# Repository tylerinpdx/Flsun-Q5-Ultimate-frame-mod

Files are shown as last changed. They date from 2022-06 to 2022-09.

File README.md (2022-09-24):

# Flsun-Q5-Ultimate-frame-mod
If you need elp or have questions, ty88#4122

The squishy wobbly motion system on the Q5 left a lot to be desired soo...

## stage 2  

keep In mind my effector is heavy ish. 182G+ 

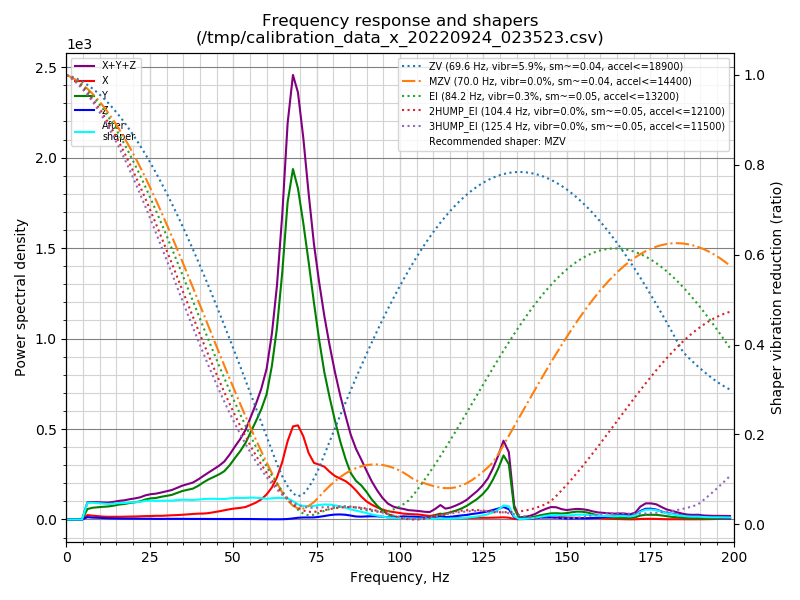
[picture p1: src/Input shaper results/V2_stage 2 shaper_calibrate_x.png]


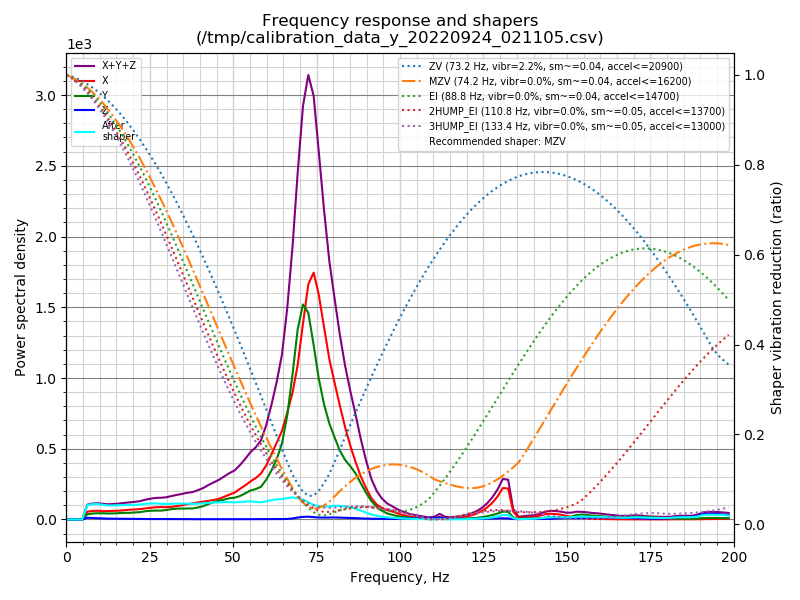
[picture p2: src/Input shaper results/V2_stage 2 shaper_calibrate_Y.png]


#### Yes this really did come from a Q5!

 

### stock tower support next to upgrade 

 

 The belt now goes all the way through the frame and into a bottom plate,
 
 Idler is held on both sides, none of that cantilever nonsense. 

 

 
In this picture the Alpha tower carriage is bottomed out against bottom tower support,
this upgrade is not supposed to reduce max printable radius but Is this **highly recommended** to reduce it to at least 96MM.

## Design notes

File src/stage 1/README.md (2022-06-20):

# Bill of materials, printing instructions and Install
The 2020 extrusion from the frame needs to fit inside the bottom tower support, so there are multiple tolerance versions.

The Idler pulley also has multiple tolerance versions, the pulley needs to have little play side to 
side otherwise it's going to rattle and make a lot of noise.

The Idler plate has a hole for a 35mm long M5 Fastener, that's should be the right size for the fastener to cut its own thread.
You could also use a 5 mm shaft.

## BOM for stage 1
- M5x16MM 12.9 12X  

- M5 t-nuts 12X These must be the larger size ones, not those twist-in nonsense things. 

- M4x50MM 12.9 6X Head diameter 7mm

- M4x22MM 12.9 3X head diameter 7 mm 

- **optional** but recommended M4 washer 9X   9 mm max diameter, max height 1.2mm

- M4 nut 9x

- M5x35MM 3X   The material doesn't matter as long as it's not pot metal.

- GT2 20T 5MM bearing idler 3X  very important, width is 8.5 mm 

- rubber feet that came with the printer and the fasteners that held the feet on. 

- bottom tower support heavy duty 3x  print it, 3MF is in stage one 

- idler plate 3x  print it, 3MF is in stage one 

## Printing instructions 
**You must have another printer to print the parts, Ideally a cartesian machine** 

ABS recommended, PETG minimum or annealed PLA For all parts, Due to proximity to the hot bed.

### bottom Tower support heavy duty
Quantity 3x

At least three layers top and bottom 

0.20MM layer height or 0.24MM layer height. <sup>Unless you have an extremely fast printer</sup>

Brim to help reduce warping to minimum, highly recommended

No support

(0.65MM extrusion width, 6 walls)  (0.40MM extrusion width, 9 walls)

Shown below is an example with 0.45MM extrusion width

Cross-section example

### idler plate
Quantity 3x

 At least four bottom layers 

Brim to help reduce warping to minimum, highly recommended

(0.65MM extrusion width, 5 walls)  (0.40MM extrusion width, 8 walls)

If you do not have good part cooling you need at least 10% infill so it doesn't collapse

If you have good part cooling you probably won't need support

Shown below is an example with 0.45MM extrusion width

plate

## Instructions

If you've already tolerance tested your other printer you can skip step 1.
----------------------------------------------------------------------------------------------------
step 1

print the tolerance tester, get it along with the instructions [here](https://github.com/tylerinpdx/Flsun-Q5-Ultimate-frame-mod/tree/main/src/tools).

after printing the tolerance tester,  take all of them and try to fit them on the extrusion of the frame, you're looking for the one that it's a little bit loose but not too loose 

Example shown below <sup> obviously your machine won't be the same </sup>

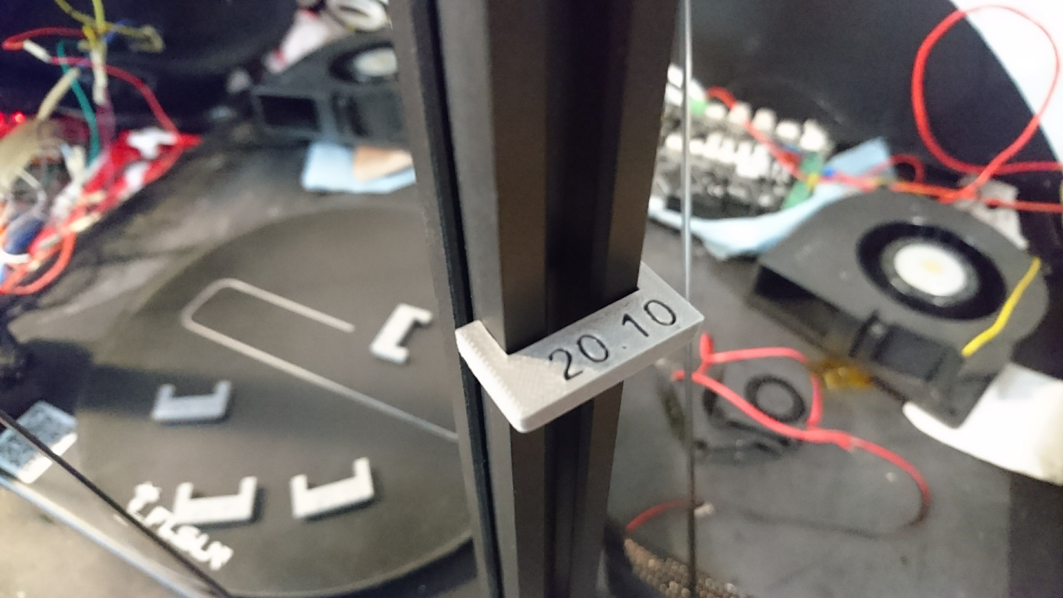
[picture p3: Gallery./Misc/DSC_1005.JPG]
test


_________________________________________________________________________________________________________________________________________________________________

step 2

After determining which one fit the best. 

Each Torrance test has a number that is the tolerance In millimeters, which corresponds with a file .3mf  

Print the one that fit the best

test

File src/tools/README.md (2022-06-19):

 The tolerance tester can be printed with 2 walls, any extrusion width is fine. 

Very important to print this without a brim. This is a difficult print so you can use like glue stick or whatever the you do to prevent it from warping, and minimal elephant foot as possible. 

**Important note** If you do not have pressure advance or linear advance you should use 4 walls to better simulate an actual print because of corner bulging 

Corner bulge example below.
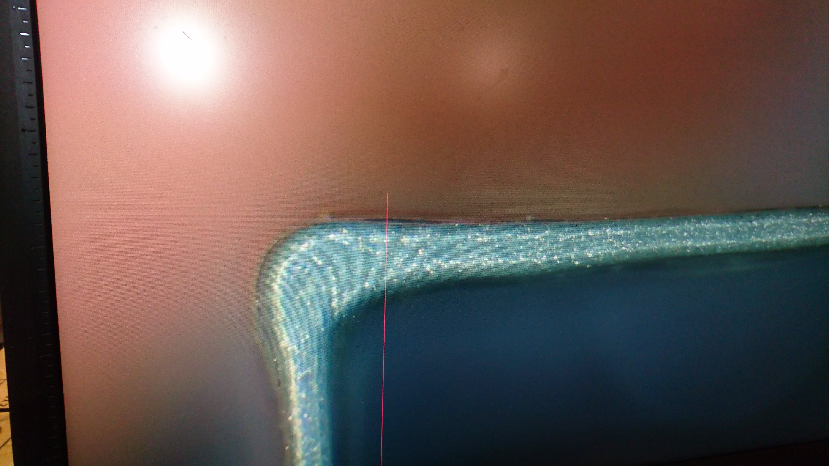
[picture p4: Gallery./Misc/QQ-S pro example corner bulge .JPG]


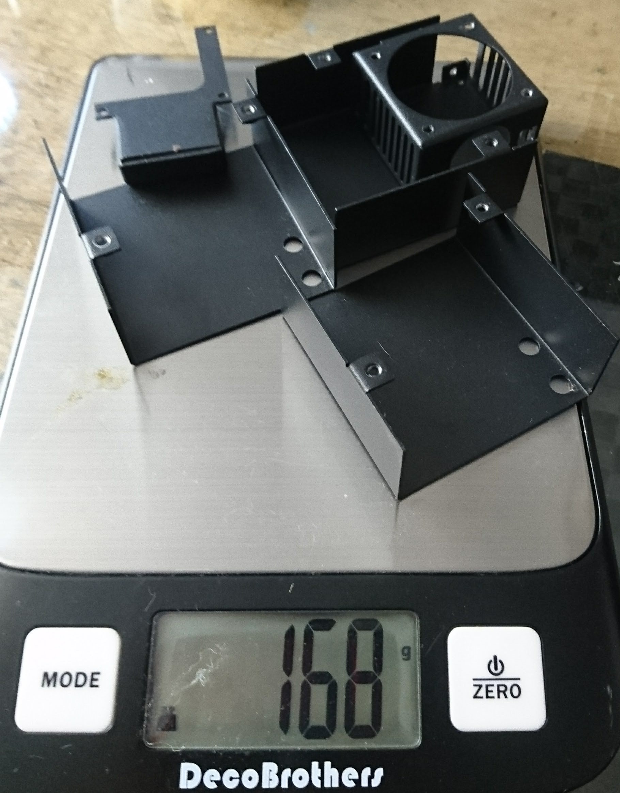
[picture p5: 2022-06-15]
weight savings .JPG

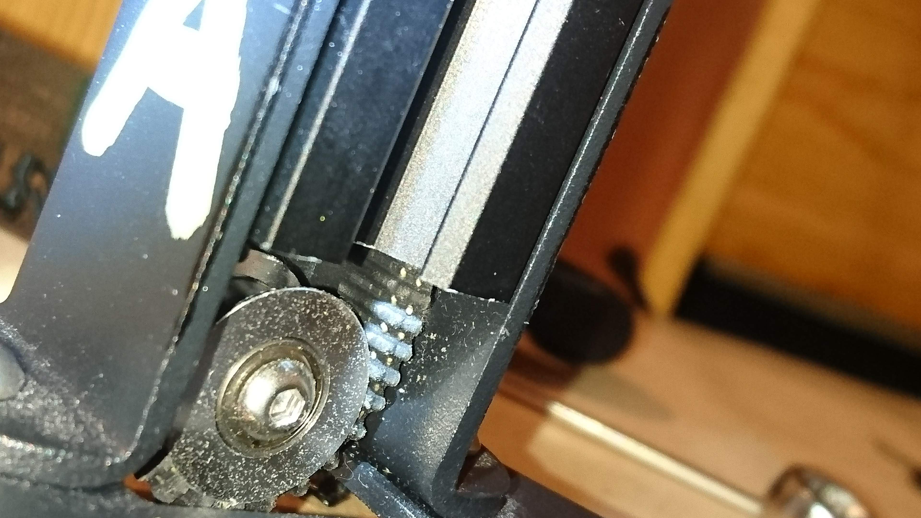
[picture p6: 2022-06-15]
stupid belt coming off of idler.JPG

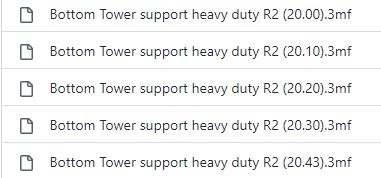
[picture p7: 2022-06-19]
Gallery./Misc/Corresponding files .JPG

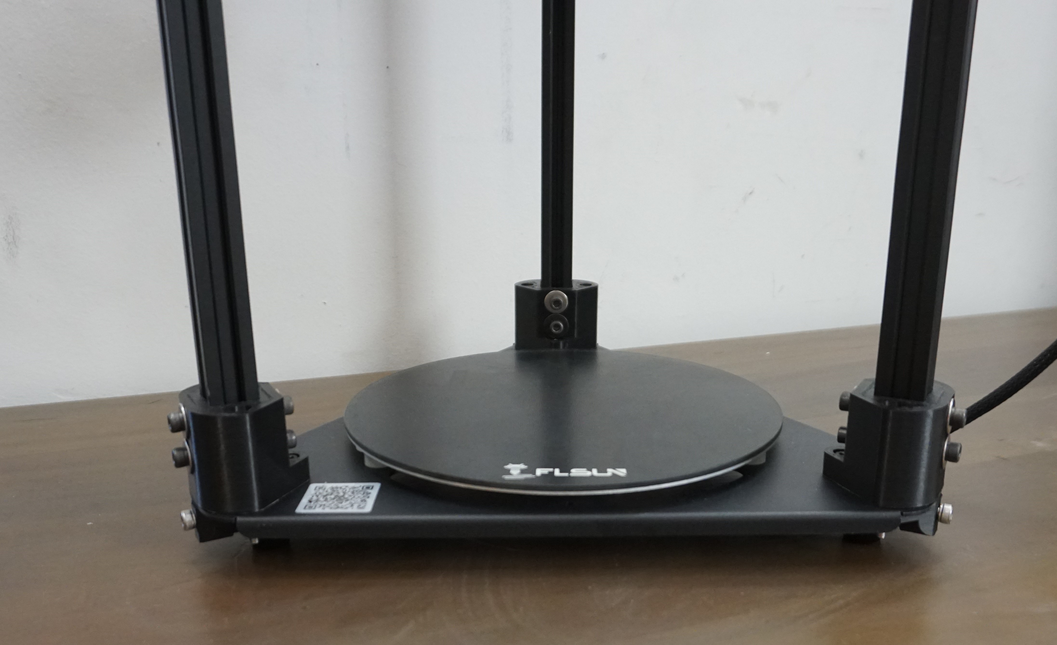
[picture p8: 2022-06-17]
Gallery./DSC06196crop.jpg

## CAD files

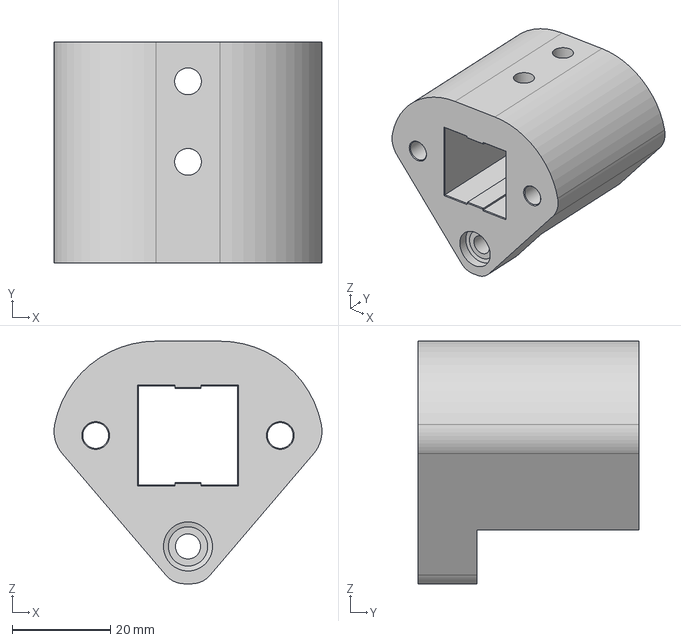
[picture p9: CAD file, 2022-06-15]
src/CAD/sizes/Bottom Tower support heavy duty R2 (20.10) v3.step
54.6 x 45.0 x 49.4 mm

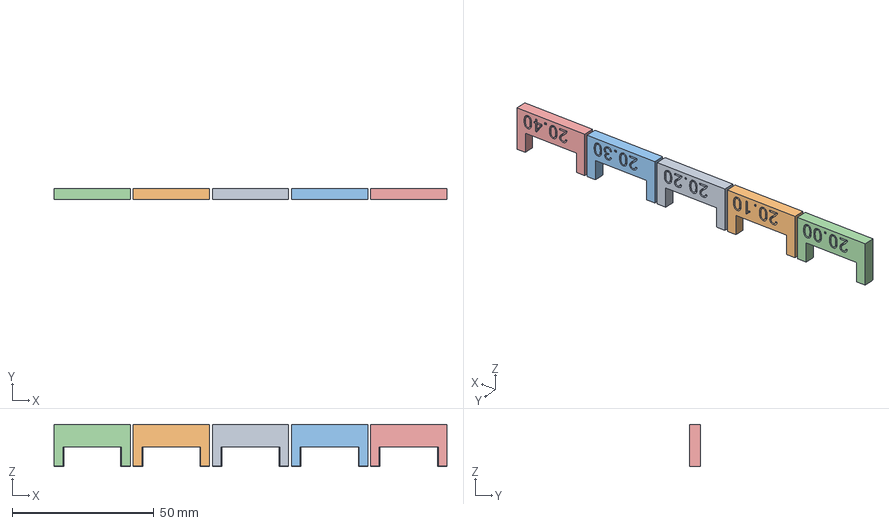
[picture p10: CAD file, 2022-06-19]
src/CAD/tolerance tester sloted v2.step
138.8 x 4.00 x 15.0 mm

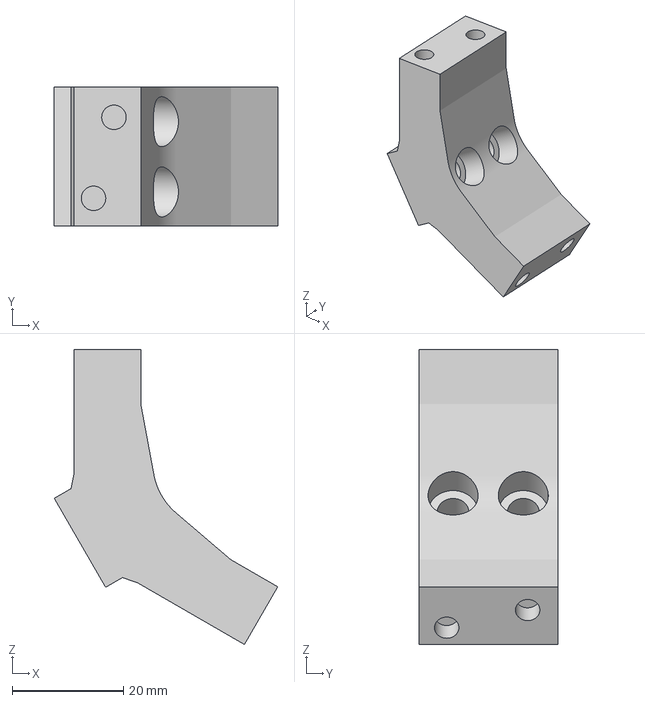
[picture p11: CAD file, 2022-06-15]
src/stage 2/cross brace mount Heat set insert v2.3mf
40.2 x 25.0 x 53.1 mm

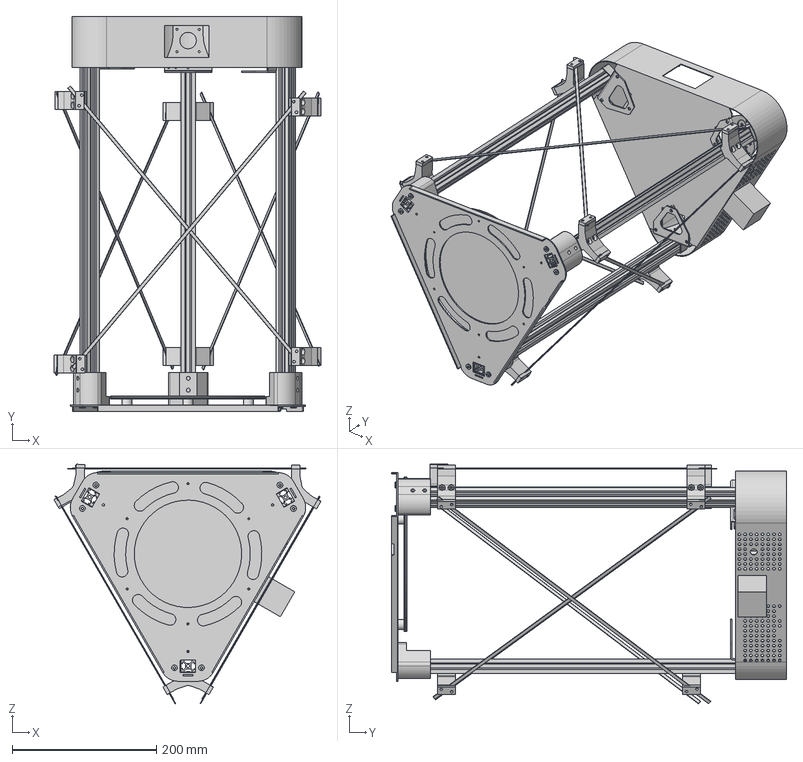
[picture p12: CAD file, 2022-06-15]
src/CAD/Reinforcement v14.step
370.6 x 548.4 x 332.6 mm
489mm 2020
489mm 2020 (1)
489mm 2020 (2)
bed
Top Tower mount v5 (1)
Top Tower mount v5 (2)
Top Tower mount v5
Bottom Tower support heavy duty R2 v5 x 3
carbon fiber strip 1x5x500MM x 6
cross brace x 6

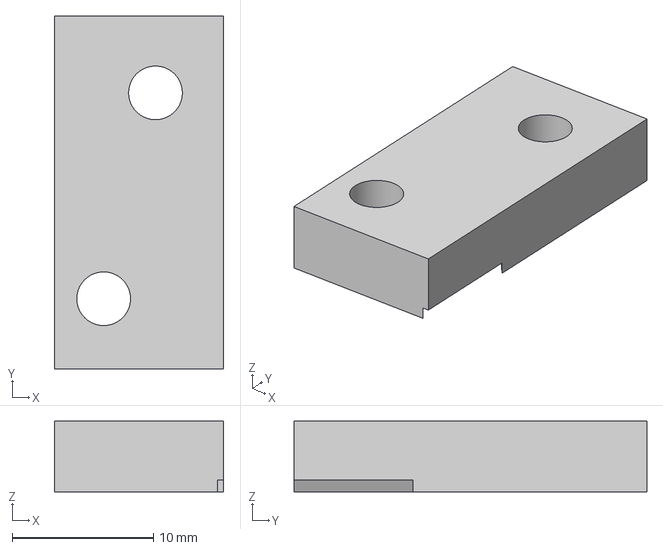
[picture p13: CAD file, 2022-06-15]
src/stage 2/cross brace clamp v2.3mf
12.0 x 25.0 x 5.00 mm

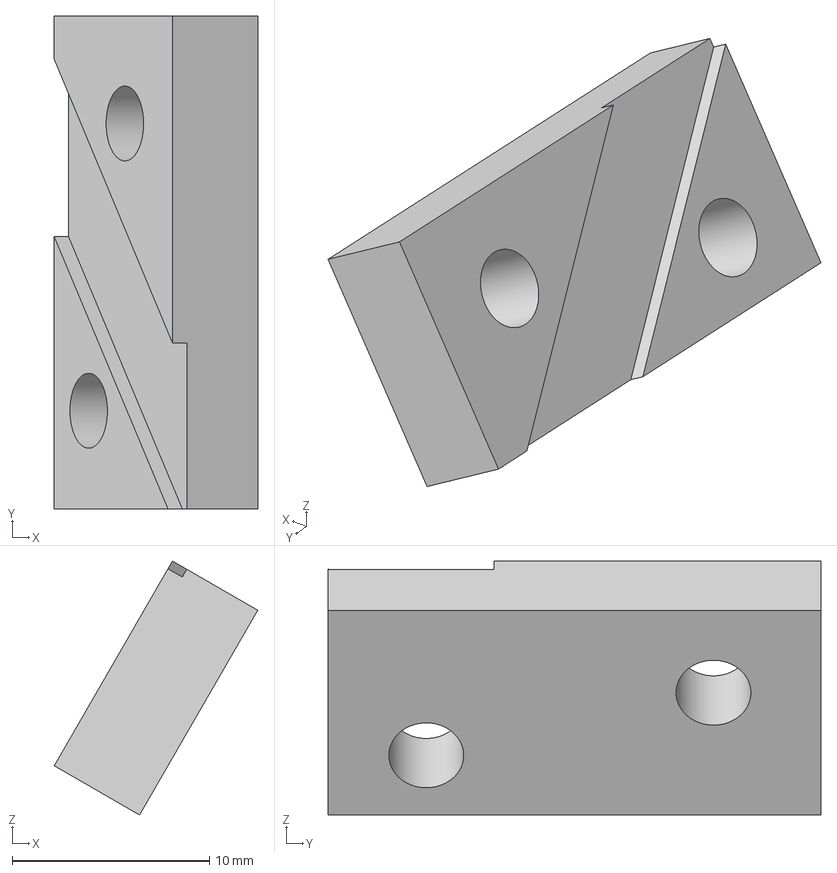
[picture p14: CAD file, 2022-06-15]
src/stage 2/cross brace clamp mirrored v2.3mf
10.3 x 25.0 x 12.9 mm

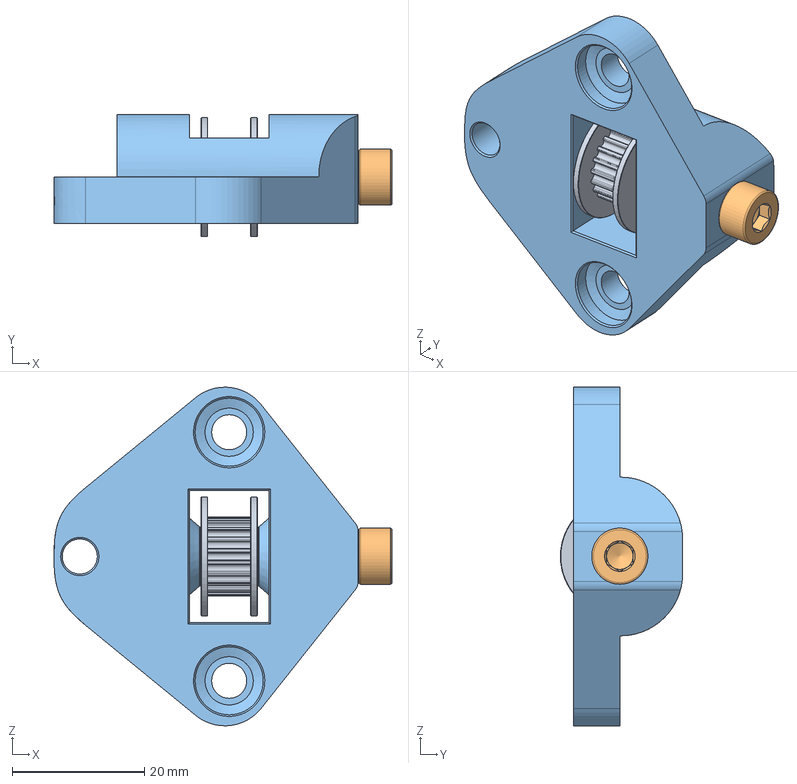
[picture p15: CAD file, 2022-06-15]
src/CAD/Idler plate R1 v7.step
51.1 x 18.5 x 51.2 mm
GT2_20T_5mmBore_10mmBelt Idler v3 v1

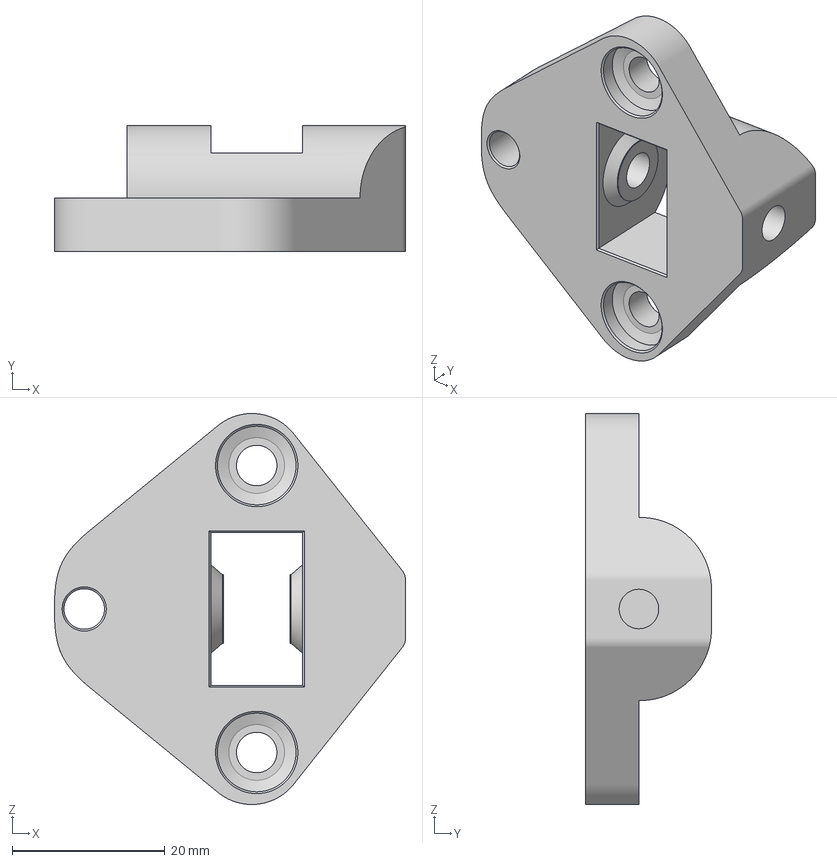
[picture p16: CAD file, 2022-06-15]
src/stage 1/idler plate R1 v2 Extremely high tolerance .3mf
46.0 x 16.5 x 51.2 mm

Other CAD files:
src/stage 1/Bottom Tower support heavy duty R2 (20.10).3mf
src/tools/tolerance tester sloted v1.stl
src/CAD/sizes/Bottom Tower support heavy duty R2 (20.30) v3.step
src/stage 1/Bottom Tower support heavy duty R2 (20.30).3mf
src/CAD/Bottom Tower support heavy duty R2 v5.step
src/CAD/sizes/Bottom Tower support heavy duty R2 (20.00) v5.step
src/stage 1/Bottom Tower support heavy duty R2 (20.43).3mf
src/CAD/sizes/Bottom Tower support heavy duty R2 (20.20) v2.step
src/stage 1/Bottom Tower support heavy duty R2 (20.00).3mf
src/stage 1/Bottom Tower support heavy duty R2 (20.20).3mf
src/CAD/Bottom Tower support heavy duty R2 v5.f3d
src/CAD/Idler plate R1 v7.f3z
src/CAD/Reinforcement v14.f3z
src/CAD/tolerance tester sloted v2.f3d

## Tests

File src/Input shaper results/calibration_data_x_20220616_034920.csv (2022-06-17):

freq | psd_x | psd_y | psd_z | psd_xyz | zv(52.8) | mzv(52.2) | ei(62.4) | 2hump_ei(44.6) | 3hump_ei(92.8)
0.0 | 0.000e+00 | 0.000e+00 | 0.000e+00 | 0.000e+00 | 1.000 | 1.000 | 1.000 | 1.000 | 1.000
1.6 | 0.000e+00 | 0.000e+00 | 0.000e+00 | 0.000e+00 | 0.995 | 0.992 | 0.991 | 0.980 | 0.988
3.2 | 0.000e+00 | 0.000e+00 | 0.000e+00 | 0.000e+00 | 0.987 | 0.982 | 0.980 | 0.950 | 0.973
4.8 | 0.000e+00 | 0.000e+00 | 0.000e+00 | 0.000e+00 | 0.978 | 0.969 | 0.965 | 0.911 | 0.955
6.3 | 4.329e+01 | 9.238e+01 | 1.177e+01 | 1.474e+02 | 0.967 | 0.953 | 0.947 | 0.863 | 0.933
7.9 | 4.938e+01 | 1.226e+02 | 9.392e+00 | 1.814e+02 | 0.953 | 0.934 | 0.927 | 0.809 | 0.908
9.5 | 5.240e+01 | 1.410e+02 | 7.576e+00 | 2.010e+02 | 0.937 | 0.913 | 0.903 | 0.748 | 0.880
11.1 | 5.427e+01 | 1.496e+02 | 6.671e+00 | 2.105e+02 | 0.920 | 0.890 | 0.878 | 0.684 | 0.850
12.7 | 5.445e+01 | 1.519e+02 | 5.850e+00 | 2.122e+02 | 0.901 | 0.864 | 0.849 | 0.616 | 0.817
14.3 | 5.492e+01 | 1.560e+02 | 5.209e+00 | 2.161e+02 | 0.879 | 0.836 | 0.819 | 0.546 | 0.783
15.9 | 5.785e+01 | 1.693e+02 | 4.208e+00 | 2.314e+02 | 0.856 | 0.807 | 0.787 | 0.476 | 0.746
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

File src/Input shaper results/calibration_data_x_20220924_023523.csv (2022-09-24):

freq | psd_x | psd_y | psd_z | psd_xyz | zv(69.8) | mzv(70.2) | ei(84.8) | 2hump_ei(104.4) | 3hump_ei(125.4)
0.0 | 0.000e+00 | 0.000e+00 | 0.000e+00 | 0.000e+00 | 1.000 | 1.000 | 1.000 | 1.000 | 1.000
1.6 | 0.000e+00 | 0.000e+00 | 0.000e+00 | 0.000e+00 | 0.996 | 0.995 | 0.994 | 0.993 | 0.992
3.2 | 0.000e+00 | 0.000e+00 | 0.000e+00 | 0.000e+00 | 0.991 | 0.988 | 0.986 | 0.984 | 0.982
4.7 | 0.000e+00 | 0.000e+00 | 0.000e+00 | 0.000e+00 | 0.985 | 0.979 | 0.977 | 0.973 | 0.970
6.3 | 2.440e+01 | 5.778e+01 | 1.311e+01 | 9.529e+01 | 0.978 | 0.969 | 0.966 | 0.960 | 0.956
7.9 | 2.115e+01 | 6.518e+01 | 1.041e+01 | 9.674e+01 | 0.969 | 0.958 | 0.954 | 0.945 | 0.940
9.5 | 1.836e+01 | 6.772e+01 | 9.528e+00 | 9.561e+01 | 0.960 | 0.945 | 0.939 | 0.929 | 0.923
11.0 | 1.593e+01 | 7.009e+01 | 8.185e+00 | 9.420e+01 | 0.949 | 0.931 | 0.924 | 0.912 | 0.904
12.6 | 1.492e+01 | 7.214e+01 | 6.586e+00 | 9.364e+01 | 0.937 | 0.915 | 0.907 | 0.893 | 0.884
14.2 | 1.513e+01 | 7.657e+01 | 5.926e+00 | 9.762e+01 | 0.924 | 0.898 | 0.889 | 0.872 | 0.862
15.8 | 1.502e+01 | 8.268e+01 | 5.362e+00 | 1.031e+02 | 0.910 | 0.880 | 0.869 | 0.850 | 0.839
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

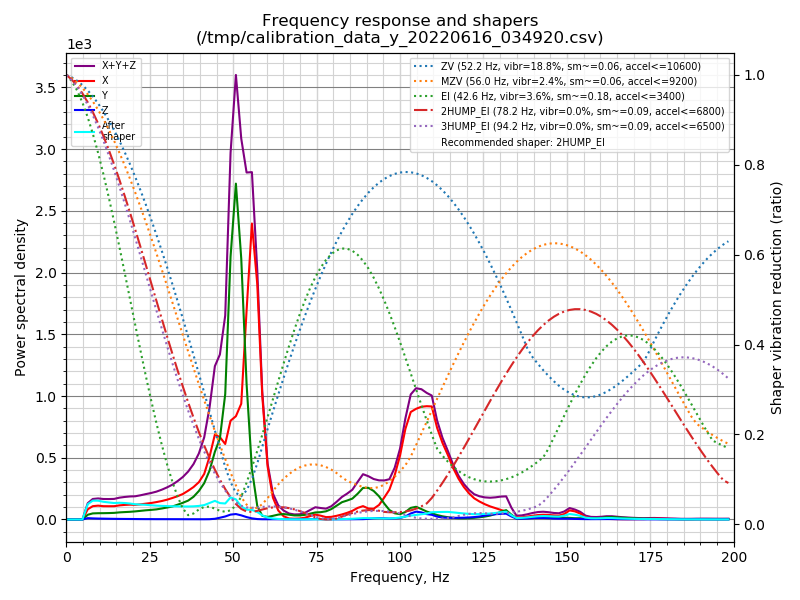
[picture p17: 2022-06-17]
Gallery./shaper_calibrate_y.png

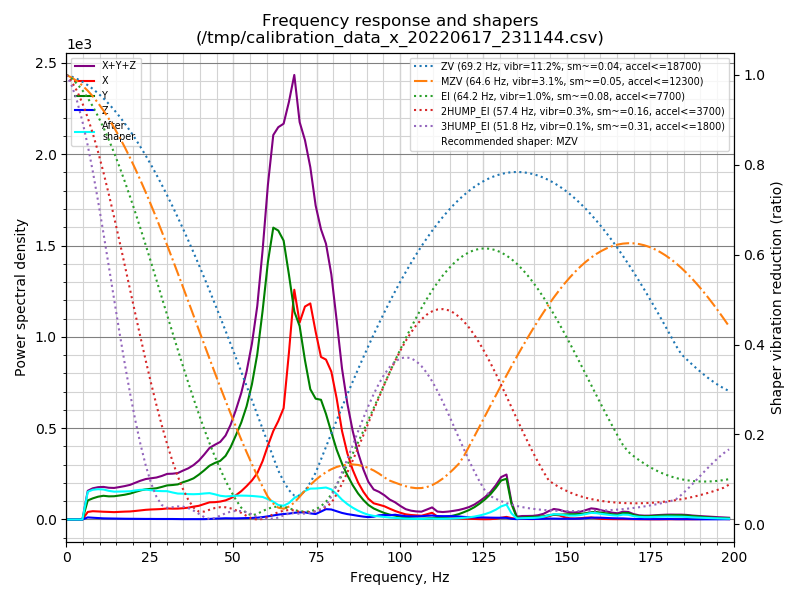
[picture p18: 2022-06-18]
src/Input shaper results/stage 2 shaper_calibrate_x.png

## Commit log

2022-06-15 Add files via upload
    Hopefully there's no screw-ups
    [Bottom Tower support heavy duty R2 high tolerance.3mf, Bottom Tower support heavy duty R2 v5.f3d, Bottom Tower support heavy duty R2 v5.step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]
2022-06-15 Add files via upload
    stage 1.8 and 2
    [Reinforcement v14.f3z, Reinforcement v14.step]
2022-06-15 Delete Bottom Tower support heavy duty R2 high tolerance.3mf
    old
    [Bottom Tower support heavy duty R2 high tolerance.3mf]
2022-06-15 Add files via upload
    sizes
    [Bottom Tower support heavy duty R2 (20.00).3mf, Bottom Tower support heavy duty R2 (20.10).3mf, Bottom Tower support heavy duty R2 (20.20).3mf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]
